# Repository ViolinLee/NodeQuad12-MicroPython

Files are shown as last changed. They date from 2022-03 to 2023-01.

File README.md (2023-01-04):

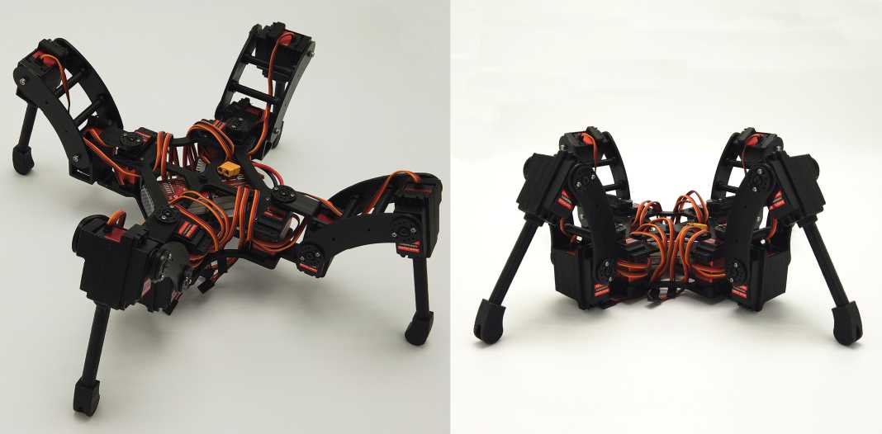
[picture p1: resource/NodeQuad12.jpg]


# NodeQuad V1
Quadruped project using NodeMCU-32S and MicroPython.   

## Brief introduction

- This project is about a spider quadruped. The robot can perform multiple gait in **MOVE** mode, and can rotate and translate with 6DOF in **POSE** mode.   
- Both **Remote control** and **Calibration** are done via `Wi-Fi` on `ESP32`.
- Brian: NodeMCU-32S (ESP32).    
- Actuator: 12 × 20Kg servo.   
- Power supply: 3S 2200mAh Lipo battery. mini360 DC-DC bulk for powering ESP32, PCA9685 and MPU6050. 8A UBEC for 12 servos. Check the PCB file for details.     
- The body is 3D printed PLA.   

## Assembly
### Fastener
Name | Spec | Required | Note
---- | ---- | --------- | -------- |
Screw | M2 * 6mm | 48 | Servo Steer : 4 x 12
Screw | M2 * 45mm | 8 | Body Base & Body Top: 2 x 4
Screw | M2.5 * 8mm | 48 | Servo Mounting: 4 x 12
Screw | M2.5 * 20mm | 8 | Tiabia Rod: 4 x 2
Screw | M3 * 65mm | 8 | Femur: 2 x 4
Screw | M3 * 10mm | 4 | Tip: 1 x 4
Screw | M3 * 12mm | 12 | Joint Axis: 1 x 12
Nuts | M2 | 8 | Body Base & Body Top: 2 x 4
Nuts (self-locking) | M3 | 12 | Joint Axis: 1 x 12 
Bearing | 684ZZ | 4 | Coxa: 1 x 4    
Bearing | 624ZZ | 8 | Femur & Tiabia: 4 + 4   

## Web Controller

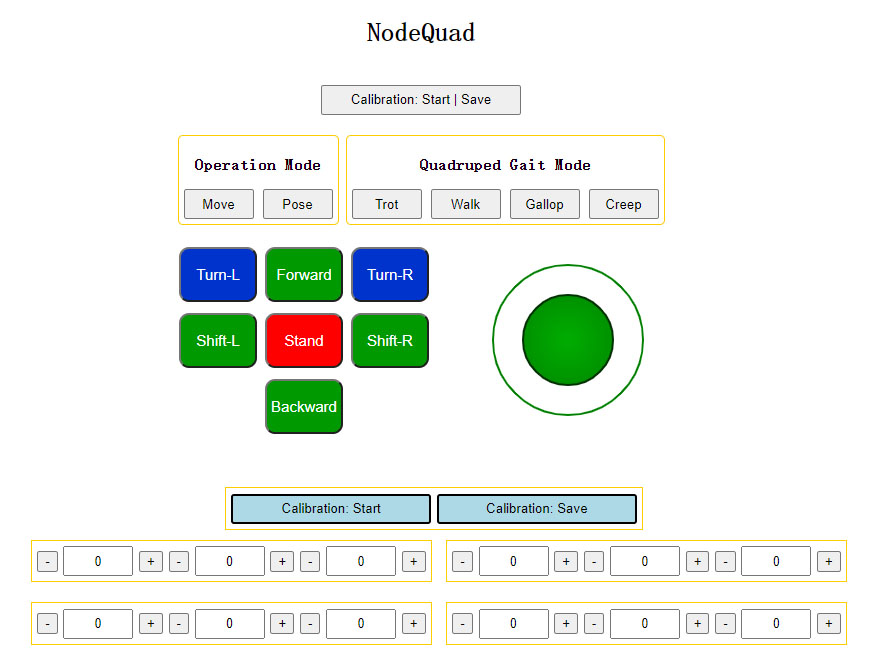
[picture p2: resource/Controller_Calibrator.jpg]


## Demonstration (Video)
[Bilibili: 【四足机器人】贴心！真香警告：18舵机的树莓派六足机器人太贵，UP主连肝数日设计制作12个舵机的ESP32四足机器人NodeQuad](https://www.bilibili.com/video/BV1RL4y1M7Cu)   
[YouTube: Open Source 3D-printed Spider Quadruped robot using ESP32 and MicroPython](https://www.youtube.com/watch?v=OmWLzTs7Svc)   

## Others   
- 项目[BOM表](resource/BOM.xlsx)参考。
 
- 业余时间捣鼓开源项目不易，望大家多多Star以支持！

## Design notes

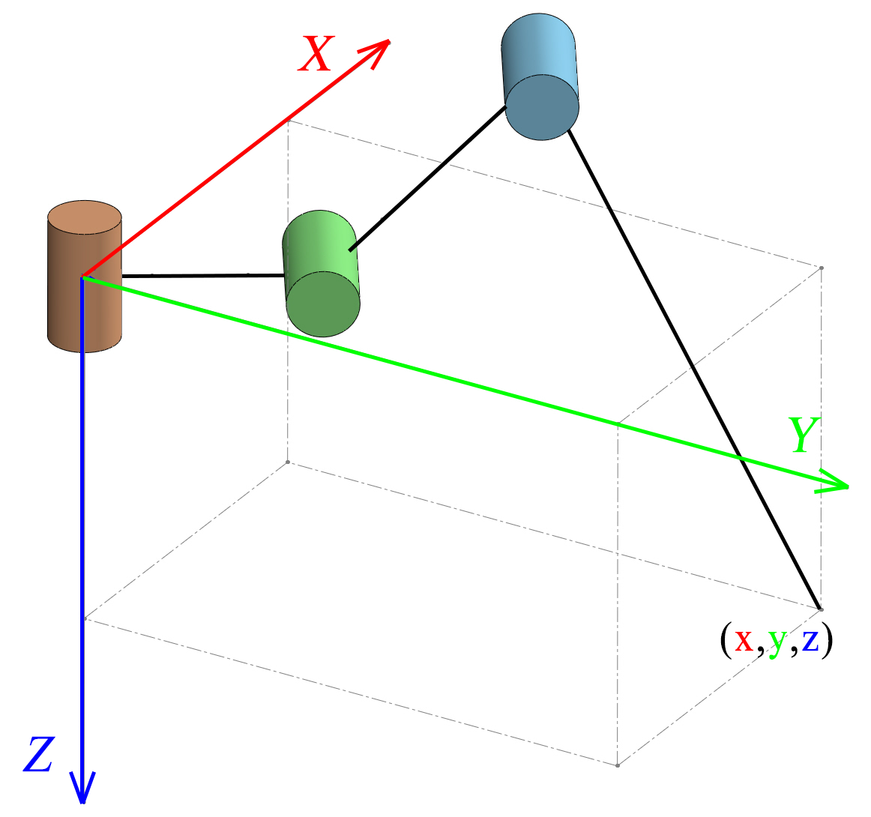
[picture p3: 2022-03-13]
resource/schematic.png

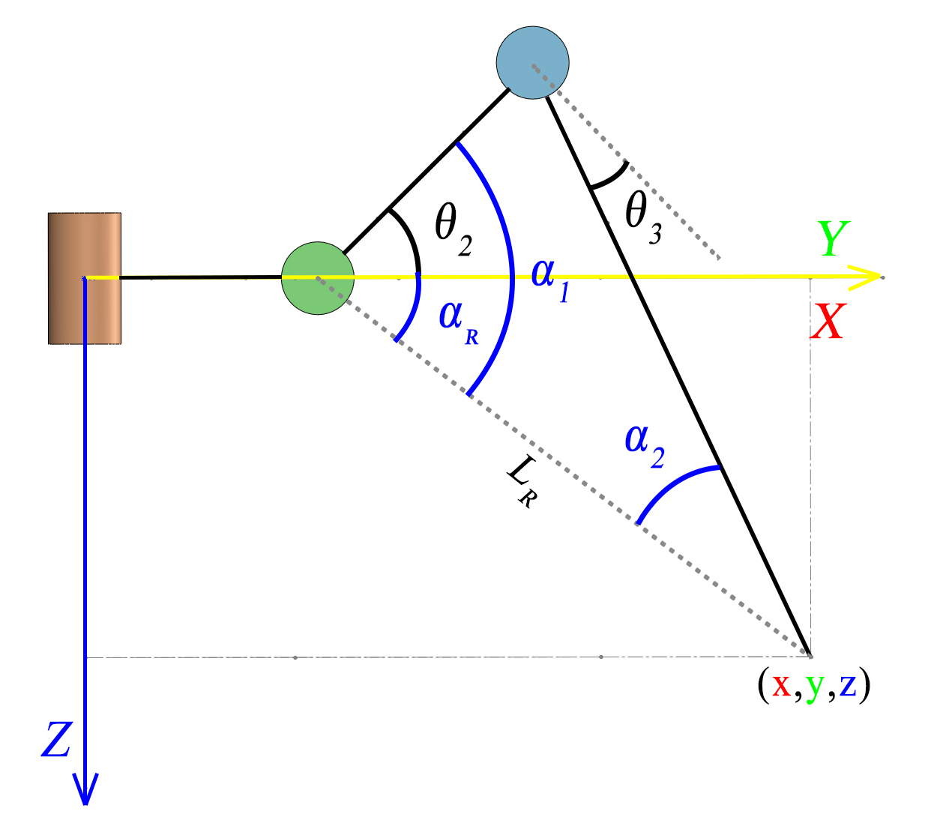
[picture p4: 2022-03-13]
resource/schematic3.png

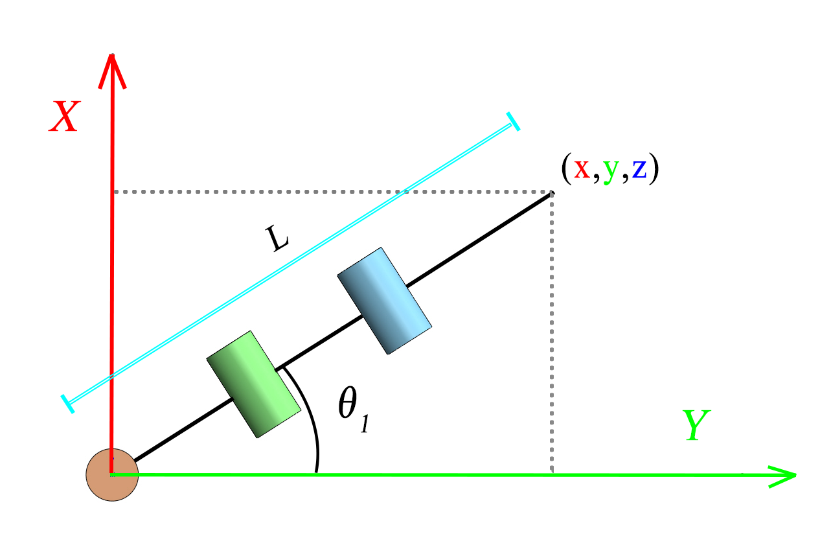
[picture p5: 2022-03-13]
resource/top.png

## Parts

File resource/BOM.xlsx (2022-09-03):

序号 | 名称 | 规格 | 数量 | 链接 | 备注
1 | 3D打印件
2 | 十字螺钉 | M2 * 6mm | 48 | https://detail.tmall.com/item.htm?id=642905715565&spm=a1z09.2.0.0.6ce32e8dihrVjI&_u=fvq3cm44aa5
3 |  | M2 * 45mm | 8
4 |  | M2.5 * 8mm | 48
5 |  | M2.5 * 20mm | 8
6 |  | M3 * 10mm | 4
7 |  | M3 * 12mm | 12
8 |  | M3 * 65mm | 8
9 | 螺母 | M2 | 12 | https://detail.tmall.com/item.htm?id=549640610734&rn=ef52c151567327f1721239872d7f2c55&abbucket=8
10 |  | M3 | 4 | https://detail.tmall.com/item.htm?id=534347662017&spm=a1z09.2.0.0.6ce32e8dihrVjI&_u=fvq3cm44411 | 自锁螺母
11 | 轴承 | 684ZZ |  | https://item.taobao.com/item.htm?id=560448857842&ns=1&abbucket=12
12 |  | 624ZZ |  | https://item.taobao.com/item.htm?spm=a1z10.3-c.w4002-15476626462.9.339f5739O8sdLk&id=544170275318
13 | TD-8120MG舵机 | 20KG | 12 | https://item.taobao.com/item.htm?id=584556271112&ns=1&abbucket=12
14 | 主控板 | NodeMCU-32S | 1 | https://detail.tmall.com/item.htm?id=658748378941&ns=1&abbucket=12&skuId=5001506878536
15 | PCA9685舵机驱动板 | 16路 |  | https://detail.tmall.com/item.htm?spm=a230r.1.14.27.2adf139eEk4jyd&id=597498156699&ns=1&abbucket=12
16 | MPU6050陀螺仪 |  |  | https://item.taobao.com/item.htm?id=16630417522&ns=1&abbucket=12
17 | SBEC独立供电模块 | 8A-16A | 1 | https://item.taobao.com/item.htm?spm=a1z09.2.0.0.6ce32e8dihrVjI&id=602114047919&_u=fvq3cm4eb51
18 | MINI360降压模块 |  |  | https://detail.tmall.com/item.htm?id=601488488830&ali_trackid=1_cedfc103b14d0bfcda29dfd2593c5113
19 | 电阻 | 680Ω | 2 | https://item.taobao.com/item.htm?id=573930462029&ns=1&abbucket=12
20 |  | 1KΩ | 1 | https://detail.tmall.com/item.htm?id=542721590093&ali_trackid=1_1ce48910c1f7eea072d2dbd3451336de
21 |  | 3KΩ | 1
22 | 直插整流二极管1N4004 | 1N4004 |  | https://detail.tmall.com/item.htm?id=41297393192&ali_trackid=1_ca0b73502bed03b7d659b5c7a7257dfa
23 | LED灯珠 | 5mm红色 | 1 | https://item.taobao.com/item.htm?spm=a1z09.8149145.0.0.3a093d85f2h7IR&id=590003354388&_u=fvq3cm42473
24 |  | 5mm蓝色 | 1
25 | AMS1117稳压模块 | 直插 | 1 | https://detail.tmall.com/item.htm?id=13301101281&spm=a1z09.2.0.0.74792e8diYGDho&_u=fvq3cm487a9
26 | 接线端子 | XT60-F | 1 | https://item.taobao.com/item.htm?spm=a1z09.2.0.0.74792e8diYGDho&id=606959435821&_u=fvq3cm40195
27 |  | KF301 | 1 | https://detail.tmall.com/item.htm?id=606681252290&spm=a1z09.2.0.0.74792e8diYGDho&_u=fvq3cm4d8c4
28 | 开关 | KCD1-101 | 1 | https://item.taobao.com/item.htm?spm=a1z09.2.0.0.74792e8diYGDho&id=564906354046&_u=fvq3cm4f6ba
29 | 排针 | 3P | 2 | https://detail.tmall.com/item.htm?id=609362740741&ali_trackid=1_acb59e7df588a8e21ea996e6e61e9ae1 | 3P即3引脚
30 |  | 1P | 6
31 |  | 8P | 1
32 | 排母 | 3P | 1 | https://detail.tmall.com/item.htm?id=41234671442&ali_trackid=1_353d47abc5ff110daad51f80abe2fcc8
33 |  | 19P | 2

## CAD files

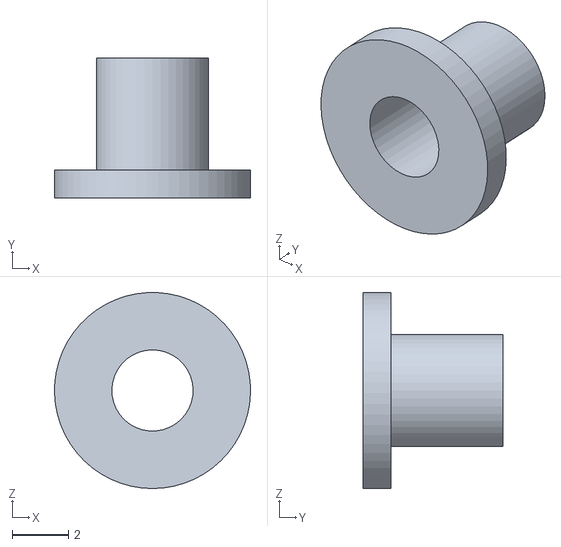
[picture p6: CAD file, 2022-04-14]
mechanism/stl/ShaftSleeve.STL
7.00 x 5.00 x 7.00

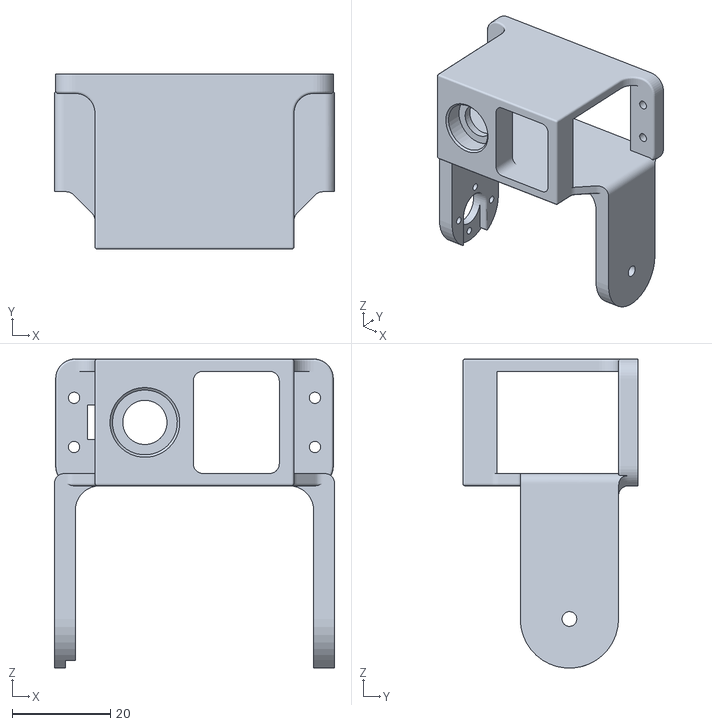
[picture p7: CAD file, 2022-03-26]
mechanism/stl/LegCoxaMirror.STL
57.0 x 35.7 x 62.9

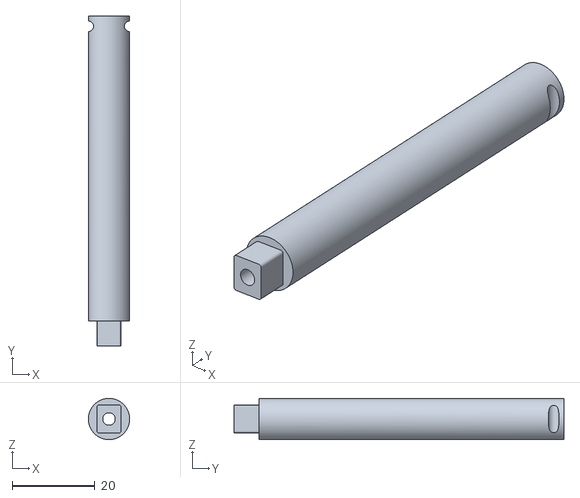
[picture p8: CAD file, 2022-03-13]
mechanism/stl/FibreRod.STL
10.0 x 80.0 x 10.0

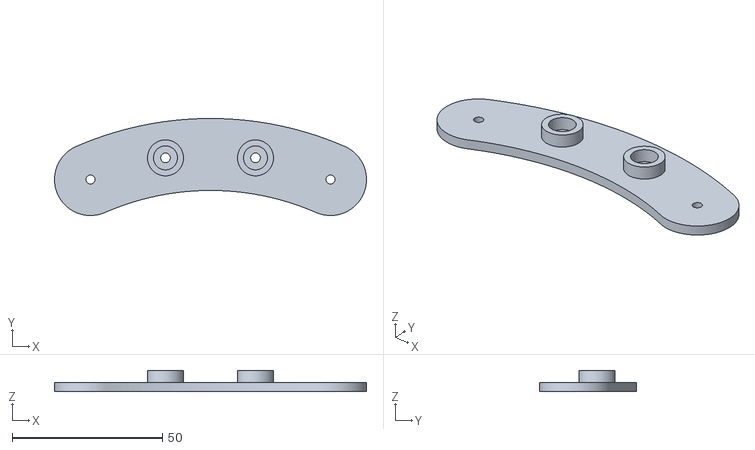
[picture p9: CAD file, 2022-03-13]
mechanism/stl/LegFumerMirror.STL
104.0 x 32.3 x 7.00

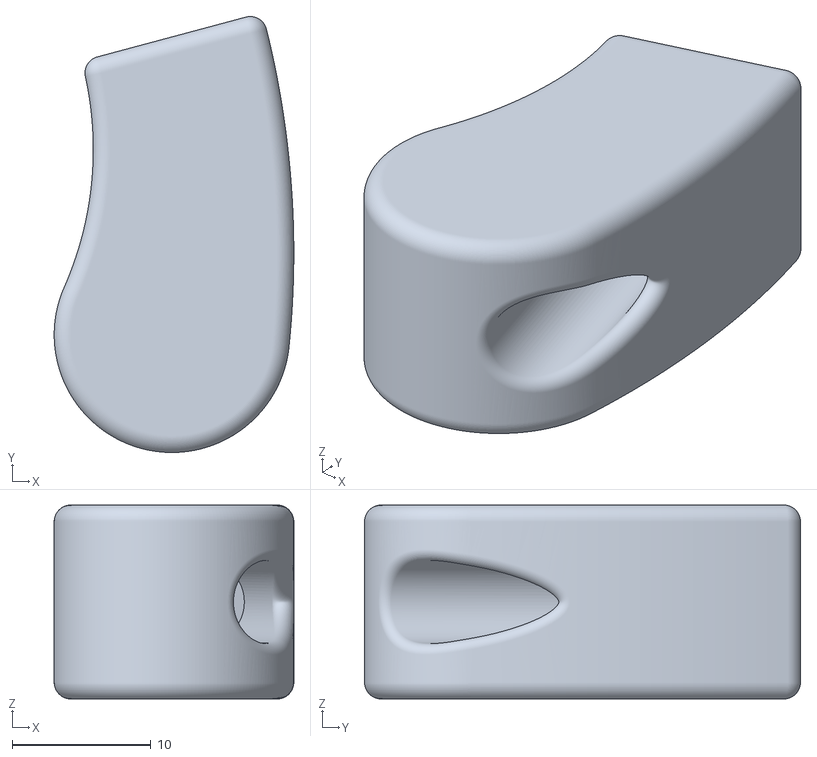
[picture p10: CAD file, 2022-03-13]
mechanism/stl/LegTip.STL
17.3 x 31.5 x 14.0

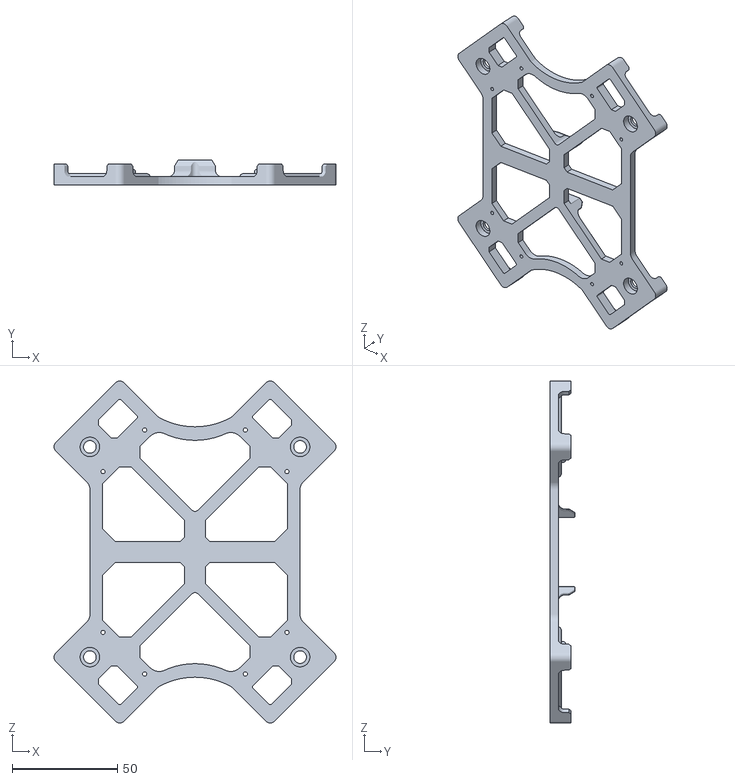
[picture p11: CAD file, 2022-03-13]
mechanism/stl/BodyBase3S.STL
134.2 x 12.0 x 162.7

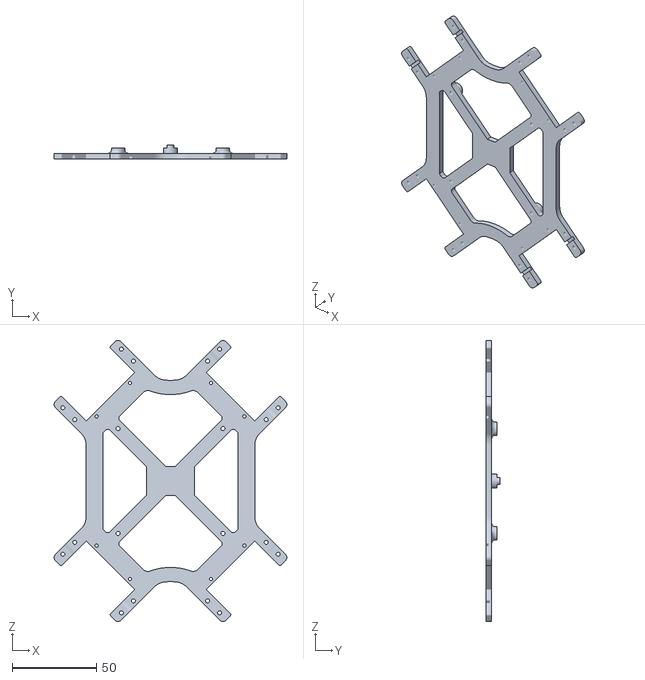
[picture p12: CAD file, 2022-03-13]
mechanism/stl/BodyTop.STL
137.7 x 8.50 x 166.3

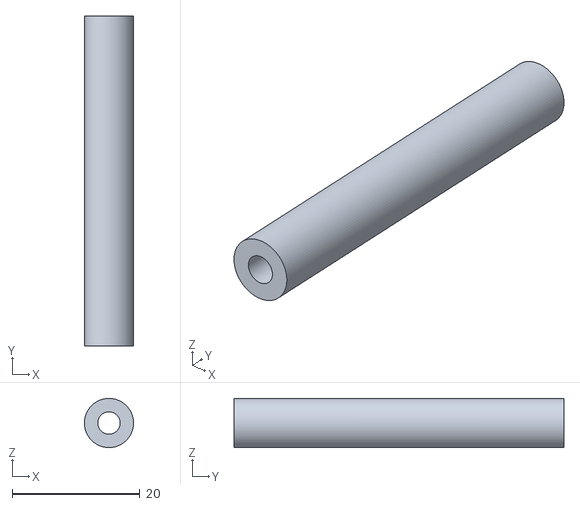
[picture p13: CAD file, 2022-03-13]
mechanism/stl/LegRod.STL
7.70 x 51.7 x 7.70

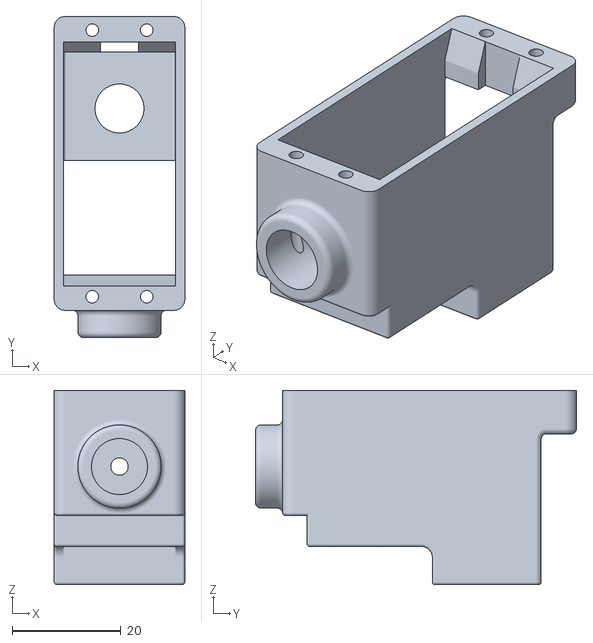
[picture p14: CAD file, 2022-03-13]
mechanism/stl/TibiaSupport.STL
24.0 x 59.0 x 35.7

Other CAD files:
mechanism/stl/LegCoxa.STL
mechanism/stl/BodyBase.STL
mechanism/stl/LegFumer.STL

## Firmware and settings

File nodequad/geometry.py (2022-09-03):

from math import cos, sin, pi

SIN30 = sin(30 * pi / 180)  # 0.5
COS30 = cos(30 * pi / 180)  # 0.866
SIN45 = sin(45 * pi / 180)  # 0.7071
COS45 = cos(45 * pi / 180)  # 0.7071
SIN15 = sin(15 * pi / 180)  # 0.2588
COS15 = cos(15 * pi / 180)  # 0.9659
SIN10 = sin(10 * pi / 180)  # 0.0872
COS10 = cos(10 * pi / 180)  # 0.9962


class FastTransform:
    @staticmethod
    def rotate45(src_point3d):
        dest = [0.0, 0.0, 0.0]
        dest[0] = src_point3d[0] * COS45 - src_point3d[1] * SIN45
        dest[1] = src_point3d[0] * SIN45 + src_point3d[1] * COS45
        dest[2] = src_point3d[2]
        return dest

    @staticmethod
    def rotate135(src_point3d):
        dest = [0.0, 0.0, 0.0]
        dest[0] = src_point3d[0] * -COS45 - src_point3d[1] * SIN45
        dest[1] = src_point3d[0] * SIN45 + src_point3d[1] * -COS45
        dest[2] = src_point3d[2]
        return dest

    @staticmethod
    def rotate225(src_point3d):
        dest = [0.0, 0.0, 0.0]
        dest[0] = src_point3d[0] * -COS45 - src_point3d[1] * -SIN45
        dest[1] = src_point3d[0] * -SIN45 + src_point3d[1] * -COS45
        dest[2] = src_point3d[2]
        return dest

    @staticmethod
    def rotate315(src_point3d):
        dest = [0.0, 0.0, 0.0]
        dest[0] = src_point3d[0] * COS45 - src_point3d[1] * -SIN45
        dest[1] = src_point3d[0] * -SIN45 + src_point3d[1] * COS45
        dest[2] = src_point3d[2]
        return dest

    @staticmethod
    def rotate90(src_point3d):
        dest = [0.0, 0.0, 0.0]
        dest[0] = src_point3d[0] * 0 - src_point3d[1] * 1
        dest[1] = src_point3d[0] * 1 + src_point3d[1] * 0
        dest[2] = src_point3d[2]
        return dest

    @staticmethod
    def rotate270(src_point3d):
        dest = [0.0, 0.0, 0.0]
        dest[0] = src_point3d[0] * 0 - src_point3d[1] * -1
        dest[1] = src_point3d[0] * -1 + src_point3d[1] * 0
        dest[2] = src_point3d[2]
        return dest


def tran2pose(Tpt):
    pass


def pos2vec(pos):
    return list(pos) + [1,]


def pose2tran(pos, orn, inv_order=False):
    """pos to homogeneous transformation matrix"""
    Tpt = [0.0] * 16  # 4 * 4
    if inv_order is False:  # T*Rz*Ry*Rx
        # first row
        Tpt[0 * 4 + 0] = cos(orn[2]) * cos(orn[1])
        Tpt[0 * 4 + 1] = cos(orn[2]) * sin(orn[1]) * sin(orn[0]) - sin(orn[2]) * cos(orn[0])
        Tpt[0 * 4 + 2] = cos(orn[2]) * sin(orn[1]) * cos(orn[0]) + sin(orn[2]) * sin(orn[0])
        Tpt[0 * 4 + 3] = pos[0]
        # second row
        Tpt[1 * 4 + 0] = sin(orn[2]) * cos(orn[1])
        Tpt[1 * 4 + 1] = sin(orn[2]) * sin(orn[1]) * sin(orn[0]) + cos(orn[2]) * cos(orn[0])
        Tpt[1 * 4 + 2] = sin(orn[2]) * sin(orn[1]) * cos(orn[0]) - cos(orn[2]) * sin(orn[0])
        Tpt[1 * 4 + 3] = pos[1]
        # third row
        Tpt[2 * 4 + 0] = -sin(orn[1])
        Tpt[2 * 4 + 1] = cos(orn[1]) * sin(orn[0])
        Tpt[2 * 4 + 2] = cos(orn[1]) * cos(orn[0])
        Tpt[2 * 4 + 3] = pos[2]
        # forth row
        Tpt[3 * 4 + 0] = 0.0
        Tpt[3 * 4 + 1] = 0.0
        Tpt[3 * 4 + 2] = 0.0
        Tpt[3 * 4 + 3] = 1.0
    else:  # Rx*Ry*Rz*T = inverse of (T*Rz*Ry*Rx)
        # first row
        Tpt[0 * 4 + 0] = cos(orn[1]) * cos(orn[2])
        Tpt[0 * 4 + 1] = -cos(orn[1]) * sin(orn[2])
        Tpt[0 * 4 + 2] = sin(orn[1])
        Tpt[0 * 4 + 3] = (cos(orn[1]) * cos(orn[2])) * pos[0] + (-cos(orn[1]) * sin(orn[2])) * pos[1] + sin(orn[1]) * \
                         pos[2]
        # second row
        Tpt[1 * 4 + 0] = cos(orn[0]) * sin(orn[2]) + sin(orn[0]) * sin(orn[1]) * cos(orn[2])
        Tpt[1 * 4 + 1] = cos(orn[0]) * cos(orn[2]) - sin(orn[0]) * sin(orn[1]) * sin(orn[2])
        Tpt[1 * 4 + 2] = -sin(orn[0]) * cos(orn[1])
        Tpt[1 * 4 + 3] = (cos(orn[0]) * sin(orn[2]) + sin(orn[0]) * sin(orn[1]) * cos(orn[2])) * pos[0] + (
                    cos(orn[0]) * cos(orn[2]) - sin(orn[0]) * sin(orn[1]) * sin(orn[2])) * pos[1] + (
                                     -sin(orn[0]) * cos(orn[1])) * pos[2]
        # third row
        Tpt[2 * 4 + 0] = sin(orn[0]) * sin(orn[2]) - cos(orn[0]) * sin(orn[1]) * cos(orn[2])
        Tpt[2 * 4 + 1] = sin(orn[0]) * cos(orn[2]) + cos(orn[0]) * sin(orn[1]) * sin(orn[2])
        Tpt[2 * 4 + 2] = cos(orn[0]) * cos(orn[1])
        Tpt[2 * 4 + 3] = (sin(orn[0]) * sin(orn[2]) - cos(orn[0]) * sin(orn[1]) * cos(orn[2])) * pos[0] + (
                    sin(orn[0]) * cos(orn[2]) + cos(orn[0]) * sin(orn[1]) * sin(orn[2])) * pos[1] + cos(orn[0]) * cos(
            orn[1]) * pos[2]
        # forth row
        Tpt[3 * 4 + 0] = 0.0
        Tpt[3 * 4 + 1] = 0.0
        Tpt[3 * 4 + 2] = 0.0
        Tpt[3 * 4 + 3] = 1.0
    return Tpt


def inv_tran(Titi):
    """finding the inverse of the homogeneous transformation matrix"""
    Titf = [0.0] * 16  # 4 * 4
    # first row
    Titf[0 * 4 + 0] = Titi[0 * 4 + 0]
    Titf[0 * 4 + 1] = Titi[1 * 4 + 0]
    Titf[0 * 4 + 2] = Titi[2 * 4 + 0]
    Titf[0 * 4 + 3] = -Titi[0 * 4 + 0] * Titi[0 * 4 + 3] - Titi[1 * 4 + 0] * Titi[1 * 4 + 3] - Titi[2 * 4 + 0] * Titi[
        2 * 4 + 3]
    # second row
    Titf[1 * 4 + 0] = Titi[0 * 4 + 1]
    Titf[1 * 4 + 1] = Titi[1 * 4 + 1]
    Titf[1 * 4 + 2] = Titi[2 * 4 + 1]
    Titf[1 * 4 + 3] = -Titi[0 * 4 + 1] * Titi[0 * 4 + 3] - Titi[1 * 4 + 1] * Titi[1 * 4 + 3] - Titi[2 * 4 + 1] * Titi[
        2 * 4 + 3]
    # third row
    Titf[2 * 4 + 0] = Titi[0 * 4 + 2]
    Titf[2 * 4 + 1] = Titi[1 * 4 + 2]
    Titf[2 * 4 + 2] = Titi[2 * 4 + 2]
    Titf[2 * 4 + 3] = -Titi[0 * 4 + 2] * Titi[0 * 4 + 3] - Titi[1 * 4 + 2] * Titi[1 * 4 + 3] - Titi[2 * 4 + 2] * Titi[
        2 * 4 + 3]
    # forth row
    Titf[3 * 4 + 0] = 0.0
    Titf[3 * 4 + 1] = 0.0
    Titf[3 * 4 + 2] = 0.0
    Titf[3 * 4 + 3] = 1.0
    return Titf


def matrix_print(matrix1d, m, n):
    for i in range(m):
        for j in range(n):
            print(matrix1d[i * n + j], end=' ')
        print('\n')


def matrix_multiply(matrix1d_left, matrix1d_right, m, p, n):
    """Matrix Multiplication Routine"""
    matrix1d_res = [0] * m * n
    for i in range(m):
        for j in range(n):
            for k in range(p):
                matrix1d_res[n * i + j] += matrix1d_left[p * i + k] * matrix1d_right[n * k + j]
    return matrix1d_res


def matrix_add(matrix1d_left, matrix1d_right, m, n):
    matrix1d_res = [0] * m * n
    for i in range(m):
        for j in range(n):
            matrix1d_res[n * i + j] = matrix1d_left[n * i + j] + matrix1d_right[n * i + j]
    return matrix1d_res


def matrix_subtract(matrix1d_left, matrix1d_right, m, n):
    return matrix_add(matrix1d_left, matrix_scale(matrix1d_right, m, n, -1), m, n)


def matrix_inverse(matrix1d, m, n):
    """预留"""
    matrix1d_inv = [0] * m * n
    return matrix1d_inv


def matrix_transpose(matrix1d, m, n):
    matrix1d_res = [0] * m * n
    for i in range(m):
        for j in range(n):
            matrix1d_res[m * j + i] = matrix1d[n * i + j]


def matrix_scale(matrix1d, m, n, k):
    """不改变传入矩阵"""
    matrix1d_res = [0] * m * n
    for i in range(m):
        for j in range(n):
            matrix1d_res[n * i + j] = matrix1d[n * i + j] * k
    return matrix1d_res


if __name__ == '__main__':
    matrix_1d = [4, 4, 4, 4, 5, 5, 5, 5, 6, 6, 6, 6, 7, 7, 7, 7]
    matrix_1d_2 = [5, 5, 5, 5, 6, 6, 6, 6, 7, 7, 7, 7, 8, 8, 8, 8]
    print(matrix_subtract(matrix_1d, matrix_1d_2, 4, 4))

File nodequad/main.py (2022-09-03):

import _thread
from utime import sleep_ms
from machine import I2C, ADC, Pin, Timer
from network import WLAN, STA_IF, AP_IF
from nodequad import NodeQuad
from setting import *
from utils import battery_monitor_loop


if __name__ == '__main__':
    # Connect to WIFI
    if wlan_sta:
        wifi = WLAN(STA_IF)
        wifi.active(True)
        wifi.connect(wifissid, wifipass)
        while not wifi.isconnected():
            pass
        wlan_ip = wifi.ifconfig()[0]
    else:
        ap = WLAN(AP_IF)
        ap.active(True)
        ap.config(essid="nodequad", password="666888999")
        ap.config(authmode=3)
        while ap.active() == False:
            pass
        wlan_ip = ap.ifconfig()[0]

    print("Listening, connect your browser to %s" % wlan_ip)

    # Quadruped Initialization
    iic = I2C(scl=Pin(pca_i2c_scl), sda=Pin(pca_i2c_sda), freq=pca_i2c_freq)
    quadruped = NodeQuad(wlan_ip, iic, pca_i2c_adr, pulse_min, pulse_max, pulse_freq)
    quadruped.init()
    sleep_ms(500)
    
    # Battery monitor routine
    adc = ADC(Pin(pin_voltage_monitor))
    adc.atten(ADC.ATTN_11DB)  # range of 3.3v
    adc.width(ADC.WIDTH_12BIT)  # 12bit accuracy
    led = Pin(pin_red, Pin.OUT)
    timer = Timer(1)
    timer.init(period=1000, mode=Timer.PERIODIC, callback=lambda t: battery_monitor_loop(adc, led, low_voltage))
    
    # Listening and update remote controller status
    _thread.start_new_thread(quadruped.web_controller.loop, ())

    # PyDog mainloop
    quadruped.main_loop()
    print("************Welcome to NodeQuad!************")

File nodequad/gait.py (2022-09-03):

from math import sin, cos, pi
from setting import p1_x, p1_y, p1_z, p2_x, p2_y, p2_z, p3_x, p3_y, p3_z, p4_x, p4_y, p4_z
from geometry import FastTransform


GAIT_TROT = 0
GAIT_WALK = 1
GAIT_GALLOP = 2
GAIT_CREEP = 3

MODE_STAND = 00
MODE_MOVE = 10
MODE_POSE = 20

MOVE_STANDBY = 11
MOVE_FORWARD = 12
MOVE_BACKWARD = 13
MOVE_LEFTSHIFT = 14
MOVE_RIGHTSHIFT = 15
MOVE_LEFTROTATE = 16
MOVE_RIGHTROTATE = 17

home_x = [p1_x, p2_x, p3_x, p4_x]
home_y = [p1_y, p2_y, p3_y, p4_y]
home_z = [p1_z, p2_z, p3_z, p4_z]


def left_rotate_path(path: list, rotation_num):
    # method 1
    rotated_path = path[rotation_num:] + path[:rotation_num]

    # method 2
    # rotated_path = [path[(i + rotation_len) % len(path)] for i, x in enumerate(path)]

    # method 3
    # from collections import deque
    # path = deque(path)
    # path.rotate(-rotation_len)
    # rotated_path = list(path)
    return rotated_path


def right_rotate_path(path: list, rotation_num):
    # method 1
    rotated_path = path[(len(path) - rotation_num):] + path[:(len([path]) - rotation_num - 1)]
    return rotated_path


class Gait:
    """步态生成"""
    def __init__(self):
        # gait constants
        self.amplitudeX, self.amplitudeY, self.amplitudeZ = 25, 15, 35
        # movement configuration
        self.frame_time_ms = 20

    def gen_path(self, gait_mode, move_status, gait_speed=0):
        """Generate gait trajectory under world frame."""
        if gait_mode == GAIT_TROT:
            path = self.trot_gait(move_status, gait_speed)
        elif gait_mode == GAIT_WALK:
            path = self.walk_gait(move_status, gait_speed)
        elif gait_mode == GAIT_GALLOP:
            path = self.gallop_gait(move_status, gait_speed)
        elif gait_mode == GAIT_CREEP:
            path = self.creep_gait(move_status, gait_speed)
        else:
            raise ValueError()
        return path

    def formated_path_status(self, fr_path_quad, br_path_quad, bl_path_quad, fl_path_quad, move_status):
        path_quad = [[fr_path_quad[path_id], br_path_quad[path_id], bl_path_quad[path_id], fl_path_quad[path_id]]
                     for path_id in range(len(fr_path_quad))]
        if move_status == MOVE_STANDBY:
            corrected_path = [[[0, 0, 0], [0, 0, 0], [0, 0, 0], [0, 0, 0]]]
        elif move_status == MOVE_FORWARD:
            corrected_path = path_quad
        elif move_status == MOVE_BACKWARD:
            corrected_path = [[[-point[0], point[1], point[2]] for point in leg_points] for leg_points in path_quad]
        elif move_status == MOVE_LEFTSHIFT:
            corrected_path = [[FastTransform.rotate270(point) for point in leg_points] for leg_points in path_quad]
        elif move_status == MOVE_RIGHTSHIFT:
            corrected_path = [[FastTransform.rotate90(point) for point in leg_points] for leg_points in path_quad]
        elif move_status == MOVE_LEFTROTATE:
            corrected_path = [[FastTransform.rotate315(leg_points[0]),
                               FastTransform.rotate45(leg_points[1]),
                               FastTransform.rotate135(leg_points[2]),
                               FastTransform.rotate225(leg_points[3])] for leg_points in path_quad]
        elif move_status == MOVE_RIGHTROTATE:
            corrected_path = [[FastTransform.rotate135(leg_points[0]),
                               FastTransform.rotate225(leg_points[1]),
                               FastTransform.rotate315(leg_points[2]),
                               FastTransform.rotate45(leg_points[3])] for leg_points in path_quad]
        else:
            raise ValueError

        path_quad_world = [[[points_set[0][0] + home_x[0], points_set[0][1] + home_y[0], points_set[0][2] + home_z[0]],
                            [points_set[1][0] + home_x[1], points_set[1][1] + home_y[1], points_set[1][2] + home_z[1]],
                            [points_set[2][0] + home_x[2], points_set[2][1] + home_y[2], points_set[2][2] + home_z[2]],
                            [points_set[3][0] + home_x[3], points_set[3][1] + home_y[3], points_set[3][2] + home_z[3]]]
                           for points_set in corrected_path]
        return path_quad_world

    def trot_gait(self, move_status, gait_speed=0):
        """global"""
        duration = 200 if gait_speed == 0 else 400
        # total ticks divided into 2 stages, 'num_ticks' = ticks per stages
        num_ticks = int(duration / self.frame_time_ms / 2)
        # fr_path_quad = [[0.0, 0.0, 0.0]] * num_ticks * 2  # shallow copy
        fr_path_quad = [[0.0, 0.0, 0.0] for i in range(num_ticks*2)]

        for stage_id in range(2):  # A cycle is divided into 2 stages
            for tick_cnt in range(num_ticks):
                interp_id = stage_id * num_ticks + tick_cnt
                if stage_id == 0:
                    fr_path_quad[interp_id][0] = -self.amplitudeX * cos(pi * tick_cnt / num_ticks)
                    fr_path_quad[interp_id][1] = 0.0
                    fr_path_quad[interp_id][2] = abs(self.amplitudeZ) * sin(pi * tick_cnt / num_ticks) * -1
                elif stage_id == 1:
                    fr_path_quad[interp_id][0] = self.amplitudeX * cos(pi * tick_cnt / num_ticks)
                    fr_path_quad[interp_id][1] = 0.0
                    fr_path_quad[interp_id][2] = 0.0
                else:
                    pass

        # Deep copy
        br_path_quad = [[point[0], point[1], point[2]] for point in right_rotate_path(fr_path_quad, num_ticks)]
        bl_path_quad = [[point[0], point[1], point[2]] for point in fr_path_quad]
        fl_path_quad = [[point[0], point[1], point[2]] for point in br_path_quad]

        path_quad_world = self.formated_path_status(fr_path_quad, br_path_quad, bl_path_quad, fl_path_quad, move_status)

        return path_quad_world

    def walk_gait(self, move_status, gait_speed=0):
        duration = 4 * 4 * self.frame_time_ms if gait_speed == 0 else 1280
        # total ticks divided into 4 stages, 'num_ticks' = ticks per stages
        num_ticks = int(duration / self.frame_time_ms / 4)
        fl_path_quad = [[0.0, 0.0, 0.0] for i in range(num_ticks*4)]
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

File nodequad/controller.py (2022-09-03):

import json
from setting import panel_html_str, calib_html_str
from socket import socket, AF_INET, SOCK_STREAM, SOL_SOCKET, SO_REUSEADDR
from gait import MODE_MOVE, MODE_POSE
from gait import GAIT_TROT, GAIT_WALK, GAIT_GALLOP, GAIT_CREEP
from gait import MOVE_STANDBY, MOVE_FORWARD, MOVE_BACKWARD, MOVE_LEFTSHIFT, MOVE_RIGHTSHIFT, MOVE_LEFTROTATE, \
    MOVE_RIGHTROTATE
from utime import sleep_ms


class WebController:
    """遥控前端逻辑和生成遥控量"""

    def __init__(self, sta_ip):
        self.sta_ip = sta_ip
        self.calibration_data = [[0.0, 0.0, 0.0] for i in range(4)]  # direct angle (rad)
        self.rc_calibration = 0
        self.rc_mode = MODE_MOVE
        self.rc_gait_mode = GAIT_TROT
        self.rc_moving_status = MOVE_STANDBY
        self.rc_pose = [0, 0, 0, 0, 0, 0]  # x, y, z, roll, pitch, yaw

    @staticmethod
    def pose_cal(component, joystick_range, rotate_range):
        pose = [int(component[i] * rotate_range/joystick_range) for i in range(len(component))]
        return pose

    def load_calibration(self, json_path):
        with open(json_path, 'r') as f:
            json_data = json.load(f)
            self.calibration_data = json_data['calibration']
        print("Load calibration data: {0}\n}".format(self.calibration_data))

    def save_calibration(self, json_path):
        with open(json_path, 'w') as f:
            json_dict = {'calibration': self.calibration_data}
            json.dump(json_dict, f)
        print("Save calibration data: {0}\n".format(self.calibration_data))

    def reset_rc_except_mode(self):
        self.rc_gait_mode = GAIT_TROT
        self.rc_moving_status = MOVE_STANDBY
        self.rc_pose = [0, 0, 0, 0, 0, 0]

    def process_panel(self, panel_req):
        try:
            header, _, json_string = panel_req.partition('\r\n\r\n')
            ctrl_quantity = json.loads(json_string)  # {'button': 'POSE', 'joy.x': 100, 'joy.x': 150, 'joy.z': 50}
        except:
            # print(panel_req)
            return
        
        button = ctrl_quantity['button'] if 'button' in ctrl_quantity.keys() else None
        joy_x = ctrl_quantity['joy.x'] if 'joy.x' in ctrl_quantity.keys() else self.rc_pose[3]
        joy_y = ctrl_quantity['joy.y'] if 'joy.y' in ctrl_quantity.keys() else self.rc_pose[4]
        joy_z = ctrl_quantity['joy.z'] if 'joy.z' in ctrl_quantity.keys() else self.rc_pose[5]
        calibration = ctrl_quantity['calibration'] if 'calibration' in ctrl_quantity.keys() else None

        if button == 'CALIBRATESTART':
            print(button)
            self.rc_calibration = 1
        elif button == 'CALIBRATESAVE':
            print(button)
            self.rc_calibration = 0
        else:
            pass

        if self.rc_calibration == 1:
            if calibration is not None:
                calibration_int = [int(str_num) for str_num in calibration]
                temp = [calibration_int[3 * i: 3 * i + 3] for i in range(4) if i % 2 == 1]
                temp_r = [calibration_int[3 * i: 3 * i + 3] for i in range(4) if i % 2 == 0]
                temp_r.reverse()
                self.calibration_data = temp + temp_r
            else:
                pass
        else:
            if button is not None and button in ['POSE', 'MOVE']:
                self.rc_mode = self.get_mode(button)
                self.reset_rc_except_mode()

            if self.rc_mode == MODE_MOVE:
                if button in ['STANDBY', 'FORWARD', 'BACKWARD', 'LEFTSHIFT', 'RIGHTSHIFT', 'LEFTTURN', 'RIGHTTURN']:
                    self.rc_moving_status = self.get_moving_status(button)
                elif button in ['TROT', 'WALK', 'GALLOP', 'CREEP']:
                    self.rc_gait_mode = self.get_gait_mode(button)
                else:
                    pass
            elif self.rc_mode == MODE_POSE:
                if button == 'STANDBY':
                    self.reset_rc_except_mode()
                elif button in ['FORWARD', 'BACKWARD', 'LEFTSHIFT', 'RIGHTSHIFT', 'LEFTTURN', 'RIGHTTURN']:
                    shift_inc = self.get_shift_increment(button)
                    for i, shift in enumerate(shift_inc[:3]):
                        self.rc_pose[i] = min(max(self.rc_pose[i] + shift, -30), 30)
                self.rc_pose[3:] = [joy_x, joy_y, joy_z]
            else:
                pass

    @classmethod
    def get_mode(cls, button):
        transitions_mode = {'POSE': MODE_POSE, 'MOVE': MODE_MOVE}
        return transitions_mode[button]

    @classmethod
    def get_gait_mode(cls, button):
        transitions_gait_mode = {'TROT': GAIT_TROT,
                                 'WALK': GAIT_WALK,
                                 'GALLOP': GAIT_GALLOP,
                                 'CREEP': GAIT_CREEP}
        return transitions_gait_mode[button]

    @classmethod
    def get_moving_status(cls, button):
        transitions_moving_status = {'STANDBY': MOVE_STANDBY,
                                     'FORWARD': MOVE_FORWARD,
                                     'BACKWARD': MOVE_BACKWARD,
                                     'LEFTSHIFT': MOVE_LEFTSHIFT,
                                     'RIGHTSHIFT': MOVE_RIGHTSHIFT,
                                     'LEFTTURN': MOVE_LEFTROTATE,
                                     'RIGHTTURN': MOVE_RIGHTROTATE}
        return transitions_moving_status[button]
    
    @classmethod
    def get_shift_increment(cls, button):
        # button in ['FORWARD', 'BACKWARD', 'LEFTSHIFT', 'RIGHTSHIFT', 'LEFTTURN', 'RIGHTTURN']
        if button == 'FORWARD':
            inc = [10, 0, 0]
        elif button == 'BACKWARD':
            inc = [-10, 0, 0]
        elif button == 'LEFTSHIFT':
            inc = [0, -10, 0]
        elif button == 'RIGHTSHIFT':
            inc = [0, 10, 0]
        elif button == 'LEFTTURN':
            inc = [0, 0, -10]
        elif button == 'RIGHTTURN':
            inc = [0, 0, 10]
        else:
            raise ValueError
        return inc

    def loop(self):
        # Setup Socket WebServer
        s = socket(AF_INET, SOCK_STREAM)
        s.setsockopt(SOL_SOCKET, SO_REUSEADDR, 1)
        s.bind((self.sta_ip, 80))
        s.listen(1)

        # Main Loop
        while True:
            try:
                # Accept request from clients
                conn, addr = s.accept()
            except OSError:
                    continue
            req = conn.recv(1024).decode()  # req = str(conn.recv(1024))
            
            # Parse Request and Process Remote Control Panel Input from Client
            self.process_panel(req)
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

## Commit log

2022-03-13 nodequad12 first commit
    [BodyBase.STL, BodyBase3S.STL, BodyTop.STL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]
2022-03-26 modify coxa hole dim
    [LegCoxa.STL, LegCoxaMirror.STL]
2022-04-14 add body base shaft sleeve
    [ShaftSleeve.STL]
2022-04-18 add assembly fastener sheet (BOM)
2022-04-19 add tail end
    [PCB_NodeQuadPCB_2022-04-19.pcbdoc]
2022-09-03 add BOM
    [BOM.xlsx, nodequad_shield_2022-03-13.schdoc]
